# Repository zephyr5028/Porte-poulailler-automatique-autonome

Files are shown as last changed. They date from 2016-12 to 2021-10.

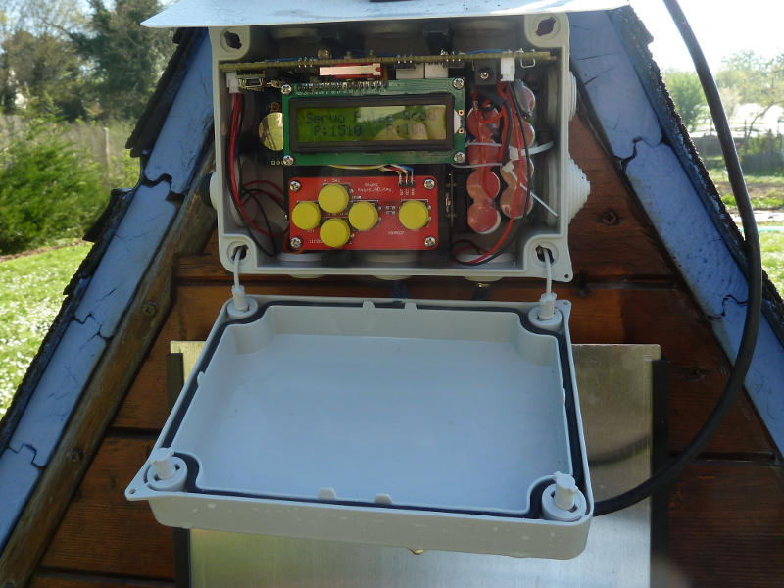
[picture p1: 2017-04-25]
avec encodeur rotatif 3eme version/boitier ouvert.JPG

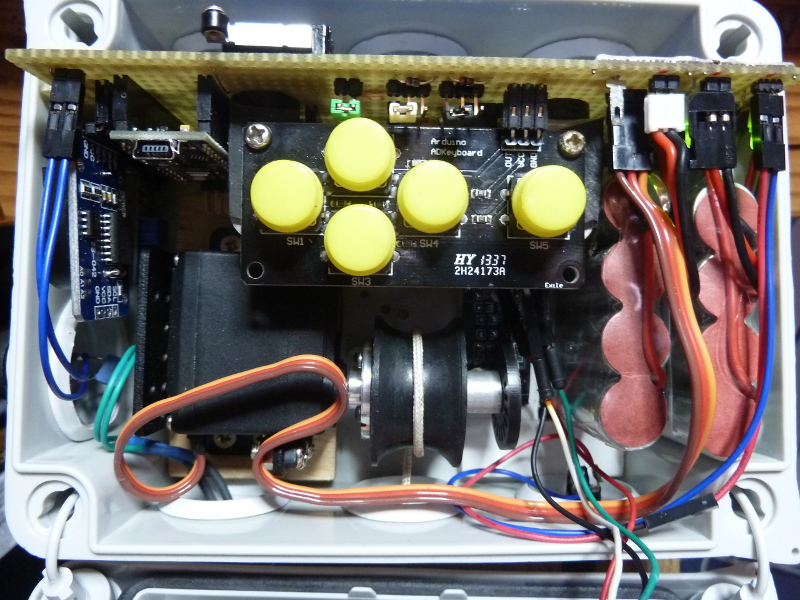
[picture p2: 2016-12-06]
avec roue optique 2eme version/boitier_prototype optique.JPG

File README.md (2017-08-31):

# Porte de poulailler automatique et autonome

Ensemble complet, autonome et reproductible par l'utilisation de l'impression 3D.

Caractéristiques :

Boitier étanche.

Porte coulissante verticale.

Alimentation par un panneau solaire et des batteries NIMH.

Déclenchement automatique de la porte par la lumière ou l’heure.

Réglage de la date et de l’heure.

Réglage de l’heure d’ouverture et de fermeture.

Réglage de la lumière pour l’ouverture et la fermeture.

Choix du type d’ouverture et de fermeture.

Affichage des réglages.

Affichage de la lumière ambiante.

Affichage de la température ambiante.

Choix (interrupteur 4) pour la transmission radio (433,92Mhz) de données de fonctionnement d'une portée d'environ 30m.

(date ; heure ; température ; tension batterie N1 ; tension batterie N2 ; lumière ambiante ; porte ouverte ou fermée ; temps de fonctionnement ; nombre de pas ;)

exemple : 5/7/17;17:4:39;33.75C;5.28V;5.31V;904L;ouv;7644ms;-1P; 

Versions :

1ere version avec un PIC16C84, ne fonctionnant pour l'ouverture/fermeture qu'avec la lumière.

2eme version avec un codeur optique, fonctionnant pour l'ouverture/fermeture avec l'heure et la lumière.

3eme version avec un codeur rotatif et l'intégration dans un boitier étanche IP55 à l'aide d'une imprimante 3D.

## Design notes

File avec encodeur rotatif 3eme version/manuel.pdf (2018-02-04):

04 février 2018

## PORTE DE POULAILLER AUTOMATIQUE

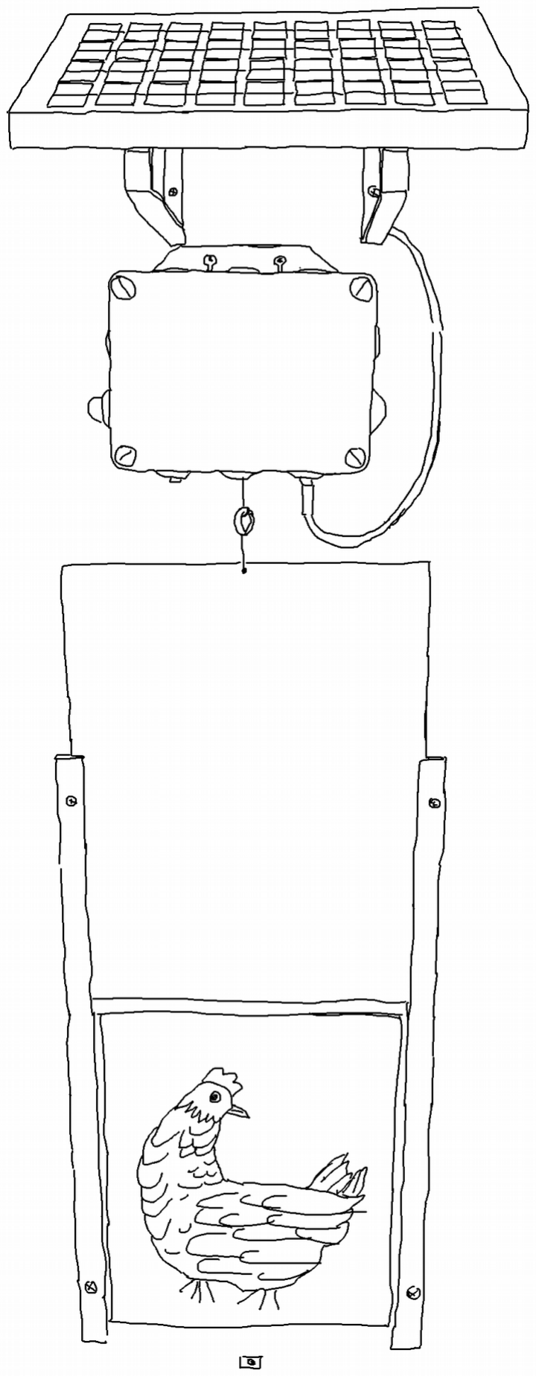
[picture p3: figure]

https://github.com/zephyr5028/Porte-poulailler-automatique | 1 / 12

- Liste du matériel
- 1 panneau solaire avec 2 supports + 4 vis / 4 chevilles.
- 1 porte dans ses 2 glissières + 4 vis / 4 chevilles.
- 1 boîtier électronique complet + 2 crochets / 2 chevilles / une clef.
- 1 protection pluie pour le boîtier.
- 1 bloc secteur 12v.
https://github.com/zephyr5028/Porte-poulailler-automatique | 2 / 12

- Caractéristiques
- Ensemble complètement autonome.
- Déclenchement automatique de la porte par la lumière ou l’heure.
- Alimentation par un panneau solaire.
- Réglage de la date et de l’heure.
- Réglage de l’heure d’ouverture et de fermeture.
- Réglage de la lumière pour l’ouverture et la fermeture.
- Choix du type d’ouverture et de fermeture.
- Affichage des réglages.
- Affichage de la lumière ambiante.
- Affichage de la température ambiante.
- Choix (interrupteur 4) de l’émission radio (433,92Mhz) de données de fonctionnement. -(portée de 30m)

(date ; heure ; température ; tension batterie N1 ; tension batterie N2 ; lumière ambiante ; porte ouverte ou fermée ;
temps de fonctionnement ; nombre de pas ;) | 5/7/17;17:4:39;33.75C;5.28V;5.31V;904L;ouv;7644ms;-1P;
https://github.com/zephyr5028/Porte-poulailler-automatique | 3 / 12

- Présentation du boîtier électronique

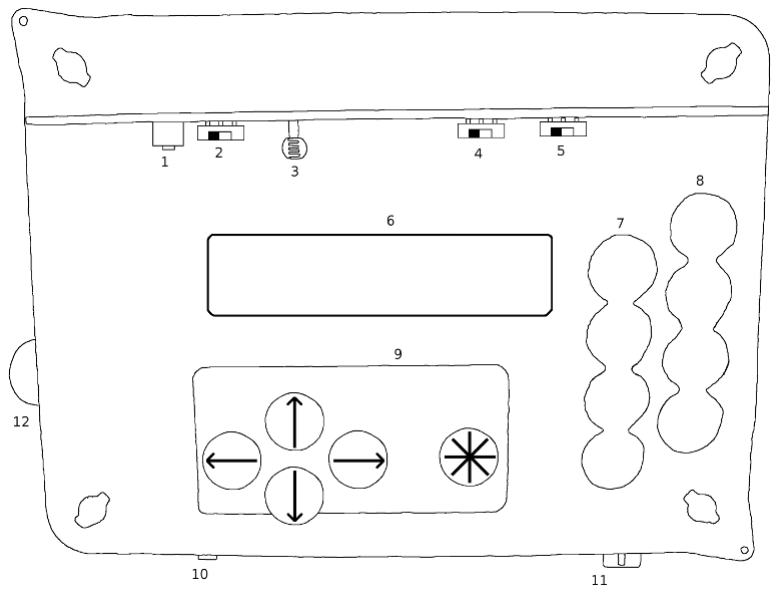
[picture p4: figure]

1 : Bouton poussoir interne pour l’ouverture ou la fermeture de la porte.

2 : Interrupteur de sélection du capteur de lumière externe (position gauche) ou interne.

3 : Capteur de lumière interne.

4 : Interrupteur : On (position droite) / Off de l’ émission de données par radio 433Mhz.

5 : Interrupteur : On (position droite) / Off du fonctionnement du boîtier.

6 : Affichage.

7 : Batterie n°1.

8 : Batterie n°2.

9 : Clavier.

10 : Capteur de lumière externe.

11 : Branchement du panneau solaire.

12 : Bouton poussoir externe pour l’ouverture ou la fermeture de la porte.

https://github.com/zephyr5028/Porte-poulailler-automatique | 4 / 12

- Installation
- - La porte doit toujours glisser librement entre les glissières.
- - Poser l’ensemble glissières et porte avec un niveau
- - Eventuellement utiliser des rondelles pour corriger les défauts du support et éviter la déformation des glissières.
- - fixer l’ensemble glissières avec vis et chevilles.
- - Lever manuellement la porte à son ouverture maximum et positionner le boîtier bien au dessus avec les crochets et chevilles.
- - Mettre en place la protection pluie dans les crochets puis tourner les crochets pour bloquer.
- - Fixer le panneau solaire avec vis et chevilles au dessus du boîtier en vérifiant la disponibilité de la longueur du câble.
- - Brancher le panneau solaire sur la prise 11.
- - Vérifier que les leds vertes sont allumées lorsque le panneau est éclairé.
- - Ouvrir le boîtier avec un tournevis plat. (ne pas forcer sur les quarts de tours)
- - Mettre sous tension (interrupteur 5) , l’aimant monte s’il était descendu.
- - Appuyer su le bouton poussoir 1 ou 12 pour descendre l’aimant.
- - Fixer la cordelette de la porte à l’aimant en gardant 1cm de jeu au dessus de la butée de la porte.
•
- - La cordelette doit toujours rester tendue.
- - Appuyer sur le bouton poussoir pour remonter la porte et vérifier son bon fonctionnement dans les glissières. La porte doit monter juste au dessus du cadre.
- - Renouveler l’opération une fois pour ajuster le réglage de la cordelette.
- - Fermer le boîtier avec un tournevis plat. (ne pas forcer sur les quarts de tours)
- Votre porte est installée.
https://github.com/zephyr5028/Porte-poulailler-automatique | 5 / 12

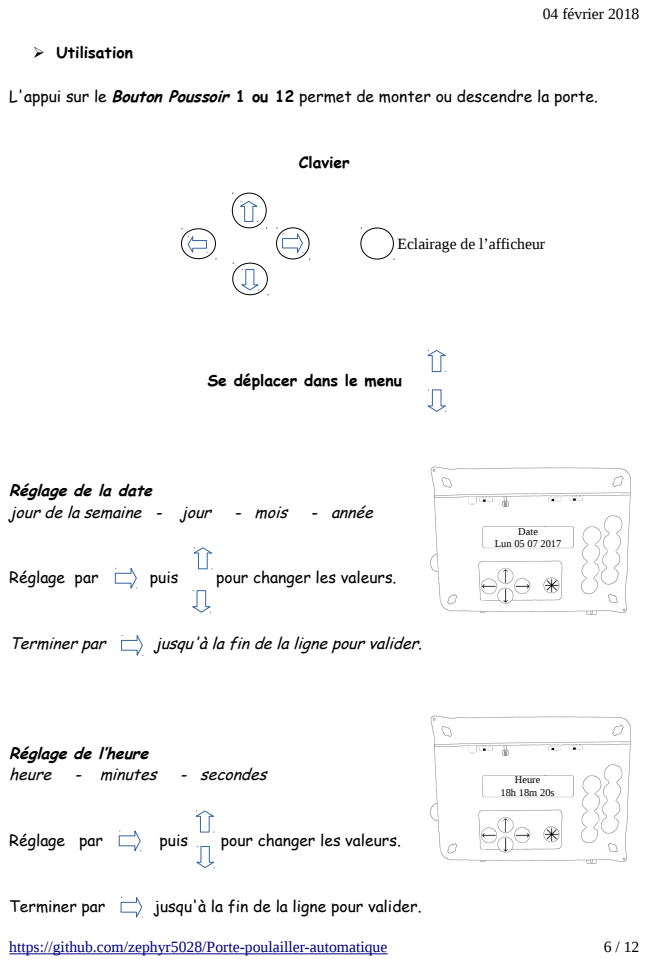
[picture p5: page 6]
➢ Utilisation; Clavier; Réglage par; puis; pour changer les valeurs.; Terminer par; jusqu'à la fin de la ligne pour valider.; https://github.com/zephyr5028/Porte-poulailler-automatique; Date Lun 05 07 2017; Heure 18h 18m 20s

L'appui sur le Bouton Poussoir 1 ou 12 permet de monter ou descendre la porte.

Eclairage de l’afficheur

Se déplacer dans le menu

Réglage de la date
jour de la semaine - jour - mois - année

Réglage de l’heure
heure - minutes - secondes

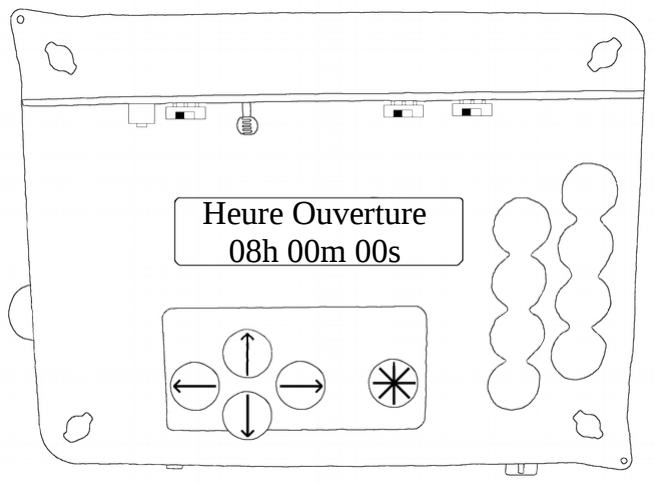
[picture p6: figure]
Heure Ouverture 08h 00m 00s

Réglage de l’heure d’ouverture de la porte
heure - minutes - secondes
Réglage par | puis | pour changer les valeurs.
Terminer par | jusqu'à la fin de la ligne pour valider.

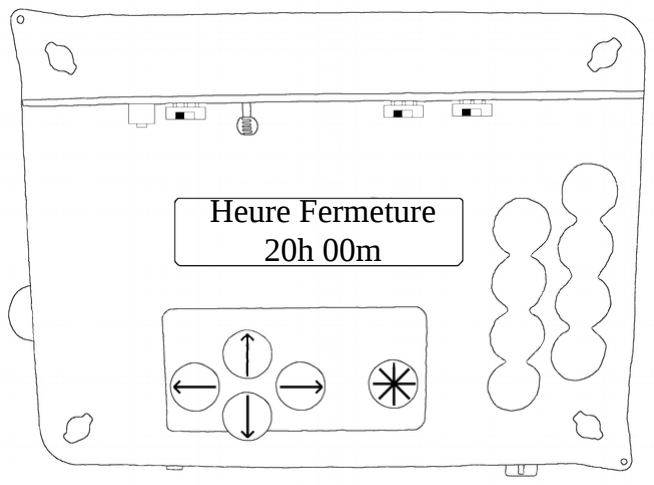
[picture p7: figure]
Heure Fermeture 20h 00m

Réglage de l’heure de fermeture de la porte heure - minutes

Réglage par | puis | pour changer les valeurs.
Terminer par | jusqu'à la fin de la ligne pour valider.

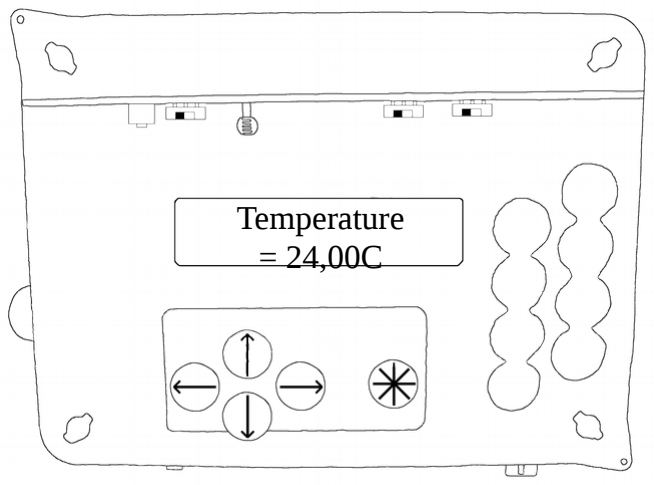
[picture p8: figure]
Temperature = 24,00C

Température ambiante
°Celcius

Capteur de température dans le circuit horloge.

Lumière ambiante
Valeur en Lux

Capteur de lumière (LDR) sous le boitier.

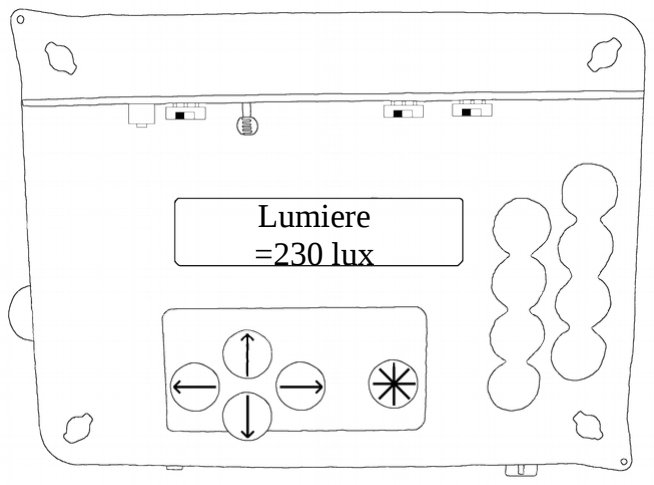
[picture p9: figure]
Lumiere =230 lux

https://github.com/zephyr5028/Porte-poulailler-automatique | 7 / 12

Réglage de la lumière du matin pour l’ouverture de la porte. Valeur en lux

Réglage par | puis | pour changer les valeurs.

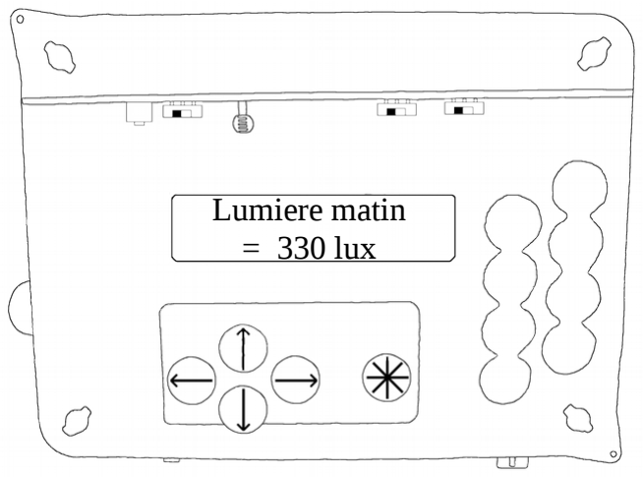
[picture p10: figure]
Lumiere matin = 330 lux

Terminer par | jusqu'à la fin de la ligne pour valider.

Réglage de la lumière du soir pour la fermeture de la porte. Valeur en lux

Réglage par | puis | pour changer les valeurs.

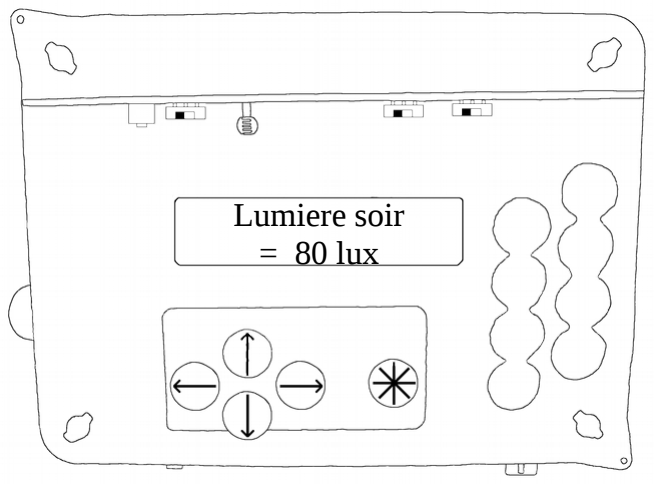
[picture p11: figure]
Lumiere soir = 80 lux

Terminer par | jusqu'à la fin de la ligne pour valider.

Choix pour l'ouverture et la fermeture

choix ouverture : heure ou lumière

choix fermeture : heure ou lumière

Réglage par | puis | pour changer les valeurs.

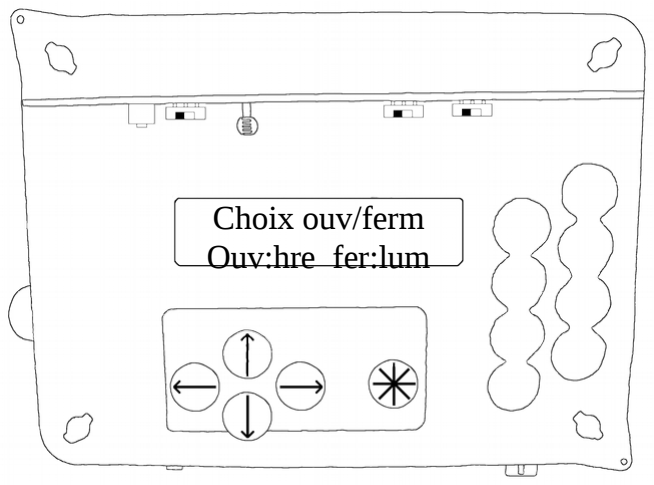
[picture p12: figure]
Choix ouv/ferm Ouv:hre fer:lum

Terminer par | jusqu'à la fin de la ligne pour valider.
https://github.com/zephyr5028/Porte-poulailler-automatique | 8 / 12

Réglage de la fin de course ouverture
(ne pas modifier si possible)
Valeur en pas correspondant à la position (de 0 à 1023)

valeur par défaut = 0 pas (aimant en haut)

Réglage par | puis | pour changer les valeurs.

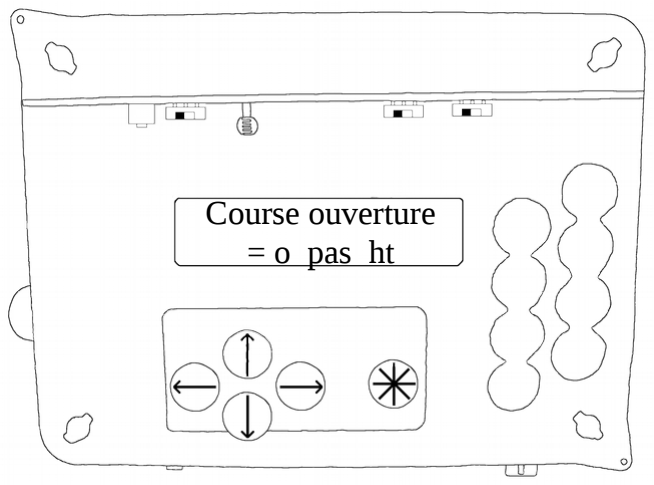
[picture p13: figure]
Course ouverture = o pas ht

Terminer par | jusqu'à la fin de la ligne pour valider.

Réglage de la fin de course fermeture
Valeur en pas correspondant à la position (de 0 à 1023)

valeur par défaut = 65 pas
(ouverture de la porte de 30cm)
Réglage par | puis | pour changer les valeurs.

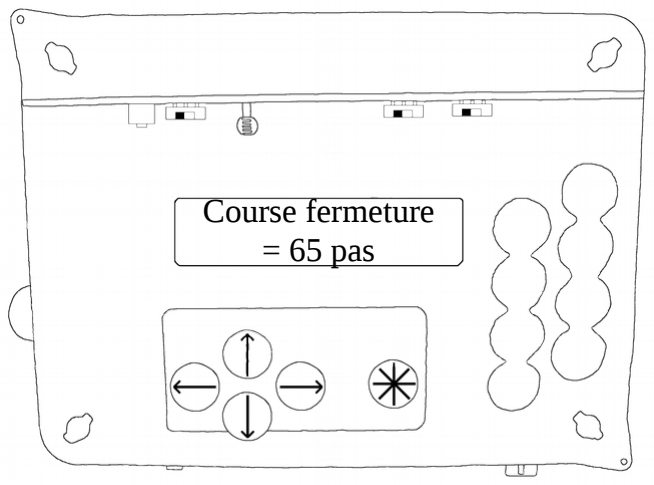
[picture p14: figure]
Course fermeture = 65 pas

Terminer par | jusqu'à la fin de la ligne pour valider.
https://github.com/zephyr5028/Porte-poulailler-automatique | 9 / 12

Tension des batteries N1 et N2
batteries de 4,8v / 2500 mAh chargée : 5,6v / déchargée : 4,4v

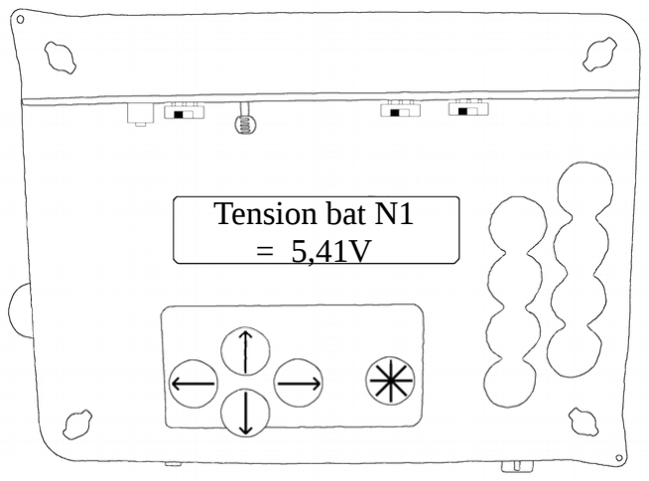
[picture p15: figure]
Tension bat N1 = 5,41V
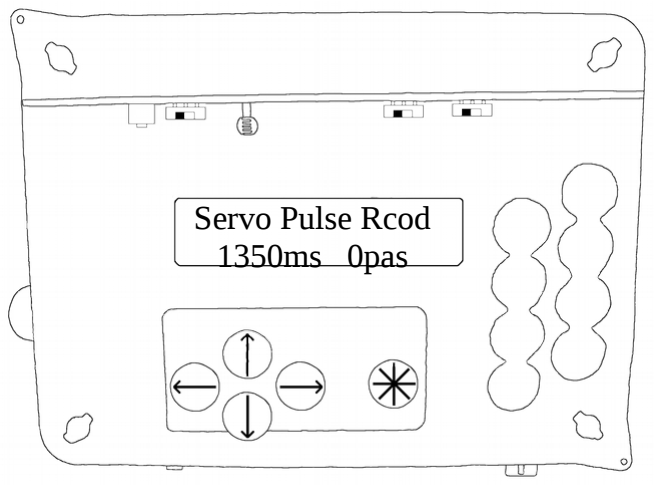
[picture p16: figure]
Servo Pulse Rcod 1350ms 0pas

Servo Pulse Rcod

P : xxxx | R : xxx

P : vitesse du servomoteur en millisecondes R : nombre de pas du servomoteur

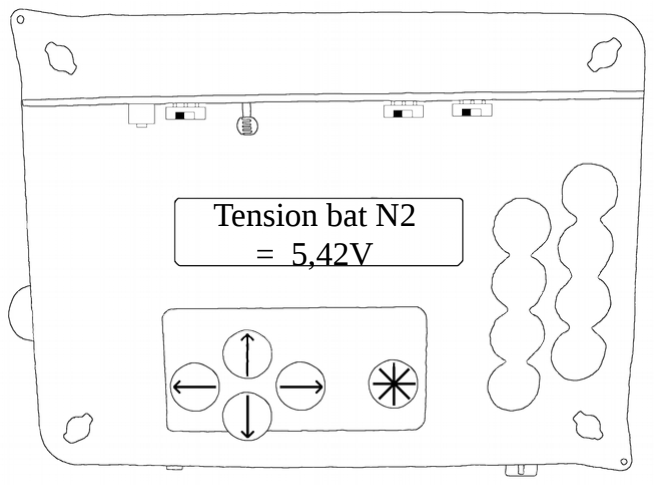
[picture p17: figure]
Tension bat N2 = 5,42V

https://github.com/zephyr5028/Porte-poulailler-automatique | 10 / 12

- Diagnostics en cas de panne
- La porte ne fonctionne plus :
- Les batteries ne sont pas suffisamment chargées par manque de lumière surtout en hiver. Utiliser le bloc secteur de 12volts pour recharger les batteries.
- Vérifier que les leds vertes sont allumées lorsque le panneau solaire est éclairé.
- Le moteur du boîtier force :
- Vérifier que la porte glisse librement dans les glissières.
https://github.com/zephyr5028/Porte-poulailler-automatique | 11 / 12

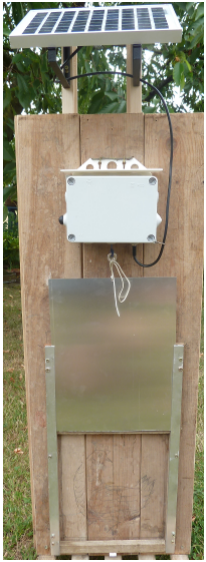
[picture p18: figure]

https://github.com/zephyr5028/Porte-poulailler-automatique | 12 / 12

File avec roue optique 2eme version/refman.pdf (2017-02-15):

## Porte du poulailler automatique

v 1.4.1

### Généré par Doxygen 1.8.11

# Table des matières

1 Porte-poulailler-automatique | 1
2 Index hiérarchique | 3
3 Index des classes | 5
4 Index des fichiers | 7
5 Documentation des classes | 9
5.1.2.1 | Accus(const byte accusPin, const float tensionMiniAccus=4.8, const float

iv | TABLE DES MATIÈRES
5.2.2.2 | Bouton(const byte pinBp, const byte pinBoitier, const int debounce=350, const
5.2.3.1 | testBoitierFerme(const volatile bool &interruptOuvBoi, const bool &boitierOuvert) | 16
5.2.3.2 | testBoitierOuvert(const volatile bool &interruptOuvBoi, const bool &boitierOuvert) 16
5.3.2.2 | Clavier(byte nbMenu, const byte pinBp, const byte pinBoitier, const int de-

Généré par Doxygen

TABLE DES MATIÈRES | v
5.3.3.1 | deplacementDansMenu(const &touche, bool &relache, const bool &reglage) . . 21
5.4.2.1 | Codeur(const byte roueCodeusePin, unsigned int finDeCourseFermeture=250, unsigned int finDeCourseOuverture=150, unsigned int compteRoue←-

vi | TABLE DES MATIÈRES
5.5.2.2 | HorlogeDS3232(const byte adresseMemoireI2C=0x57, const byte m_rtcINT=5,
5.5.3.3 | choixTypeOuvertureFermeture(bool choixOuvertureFermeture, const byte alarme) 34

TABLE DES MATIÈRES | vii

5.5.3.18 sauvEepromChoix(unsigned int valeurChoix, const bool matinSoirOuvFerm,

5.6.3.2 | affichageDateHeure(String jourSemaine, byte jourHeure, byte moisMinute, byte
5.6.3.3 | affichageLumFinCourse(unsigned int lum, byte ligne, bool siNonReglable=0) . . 46

viii | TABLE DES MATIÈRES

5.6.3.10 cursorPositionReglages(const byte &touche, bool &relache, bool &reglage, const

5.7.2.1 | LcdPCF8574(char, const byte taille=16, const byte nbLigne=2, boolean de-
5.7.3.2 | affichageDateHeure(String jourSemaine, byte jourHeure, byte moisMinute, byte
5.7.3.3 | affichageLumFinCourse(unsigned int lum, byte ligne, bool siNonReglable=0) . . 56

TABLE DES MATIÈRES | ix

5.7.3.10 cursorPositionReglages(const byte &touche, bool &relache, bool &reglage, const

5.8.2.1 Lumiere(const byte lumierePin, unsigned int lumMatin, unsigned int lumSoir, const byte heureFenetreSoir=17, const float rapportConvertion=5, const byte temps←-

x | TABLE DES MATIÈRES
5.8.3.9 | nonDeclenchementPositionServo(volatile unsigned int compteRoueCodeuse, un-

5.8.3.11 set_m_compteurWatchdogLumiere(unsigned int compteurWatchdogLumiere) . . 69

TABLE DES MATIÈRES | xi
5.9 Référence de la classe PowerTools | 73
5.9.1 Description détaillée | 74
5.9.2 Documentation des constructeurs et destructeur | 74
5.9.2.1 | PowerTools() | 74
5.9.2.2 | PowerTools(const boolean debug=false) | 74
5.9.2.3 | ∼PowerTools() | 74
5.9.3 Documentation des fonctions membres | 75
5.9.3.1 | setup_watchdog(int parametreTemps) | 75
5.9.3.2 | setupPower() | 75
5.9.3.3 | tailleChaine(char ∗chaine) | 75
5.9.4 Documentation des données membres | 76
5.9.4.1 m_debug | 76
5.10 Référence de la classe Radio | 76
5.10.1 Description détaillée | 77
5.10.2 Documentation des constructeurs et destructeur | 77

5.10.2.1 Radio(byte pinEmRadio, byte pinSwitchEmissionRadio, int vitesseTransmission,
| byte taille, boolean radio=false, boolean debug=false) | 77
5.10.2.2 ∼Radio() | 77
5.10.3 Documentation des fonctions membres | 78
5.10.3.1 chaineVide() | 78
5.10.3.2 envoiFloat(float valeur, boolean boitierOuvert=true, char ∗texte="""") | 78
5.10.3.3 envoiMessage(char ∗chaine1) | 79

5.10.3.4 envoiUnsignedInt(unsigned int valeur, boolean boitierOuvert=true, char ∗texte="""") 80

5.10.3.5 get_m_radio() | 80
5.10.3.6 init() | 81
5.10.3.7 messageRadio(char ∗chaine1) | 81
5.10.3.8 messageSansParametre() | 82
5.10.3.9 raz_m_chaine() | 82
5.10.3.10 set_m_radio(bool radio) | 83
5.10.3.11 testSwitchEmissionRadio() | 83
5.10.4 Documentation des données membres | 83

xii | TABLE DES MATIÈRES
5.10.4.1 m_chaine | 83
5.10.4.2 m_debug | 83
5.10.4.3 m_pinEmRadio | 83
5.10.4.4 m_pinSwitchEmissionRadio | 84
5.10.4.5 m_radio | 84
5.10.4.6 m_taille | 84
5.10.4.7 m_vitesseTransmission | 84
5.11 Référence de la classe ServoMoteur | 84
5.11.1 Description détaillée | 87
5.11.2 Documentation des constructeurs et destructeur | 87
5.11.2.1 ServoMoteur(const byte pinCde, const byte pinRelais, const byte pinSecurite←-Haute, const int pulseStop=1500, const int pulseOuvFerm=140, const int pulse←-
Reduit=70, boolean debug=false) | 87
5.11.2.2 ∼ServoMoteur() | 87
5.11.3 Documentation des fonctions membres | 88
5.11.3.1 get_m_ouvFerm() | 88
5.11.3.2 get_m_pulse() | 88
5.11.3.3 get_m_servoAction() | 88
5.11.3.4 init() | 89
5.11.3.5 modificationVitesse(bool reduit) | 89
5.11.3.6 relaisHorsTension() | 90
5.11.3.7 relaisSousTension() | 90
5.11.3.8 servoHorsTension(unsigned int compteRoueCodeuse, unsigned int finCourse←-
Ouverture) | 91
5.11.3.9 servoOuvFerm(bool batterieFaible, bool reduit) | 92
5.11.3.10 servoVitesse(bool reduit) | 92
5.11.3.11 set_m_ouvFerm(bool ouvFerm) | 93
5.11.3.12 set_m_pulse(int pulse) | 94
5.11.3.13 set_m_servoAction(bool servoAction) | 94
5.11.4 Documentation des données membres | 94
5.11.4.1 m_debug | 94
5.11.4.2 m_ouvFerm | 94
5.11.4.3 m_pinCde | 94
5.11.4.4 m_pinRelais | 94
5.11.4.5 m_pinSecuriteHaute | 94
5.11.4.6 m_pulse | 94
5.11.4.7 m_pulseOuvFerm | 95
5.11.4.8 m_pulseReduit | 95
5.11.4.9 m_pulseStop | 95
5.11.4.10 m_servoAction | 95

TABLE DES MATIÈRES | xiii
6 Documentation des fichiers | 97

6.1 Référence du fichier /home/jlm-atelier/Bureau/GIT/Porte-poulailler-automatique/carte heuristique

6.2 Référence du fichier /home/jlm-atelier/Bureau/GIT/Porte-poulailler-automatique/porte_poulailler_←-

6.3 Référence du fichier /home/jlm-atelier/Bureau/GIT/Porte-poulailler-automatique/porte_poulailler_←-

xiv | TABLE DES MATIÈRES
6.3.1.25 openTime() | 115
6.3.1.26 ouverturePorte() | 116
6.3.1.27 ouvFermLum() | 117
6.3.1.28 read_temp(const boolean typeTemperature) | 118
6.3.1.29 regFinDeCourseFermeture() | 119
6.3.1.30 regFinDeCourseOuverture() | 120
6.3.1.31 reglageDate() | 120
6.3.1.32 reglageHeureFermeture() | 121
6.3.1.33 reglageHeureOuverture() | 121
6.3.1.34 reglageTime() | 122
6.3.1.35 routineGestionWatchdog() | 123
6.3.1.36 routineInterrruptionAlarme2() | 123
6.3.1.37 routineInterruptionAlarme1() | 124
6.3.1.38 routineInterruptionBp() | 125
6.3.1.39 routineTestFermetureBoitier() | 125
6.3.1.40 routineTestOuvertureBoitier() | 126
6.3.1.41 temporisationAffichage(const int boucleTemps) | 126
6.3.1.42 testServo() | 127

6.4 Référence du fichier /home/jlm-atelier/Bureau/GIT/Porte-poulailler-automatique/porte_poulailler_←-
affichage_clavier_rtc/Accus.cpp | 128

6.5 Référence du fichier /home/jlm-atelier/Bureau/GIT/Porte-poulailler-automatique/porte_poulailler_←-
affichage_clavier_rtc/Accus.h | 128

6.6 Référence du fichier /home/jlm-atelier/Bureau/GIT/Porte-poulailler-automatique/porte_poulailler_←-
affichage_clavier_rtc/Bouton.cpp | 129

6.7 Référence du fichier /home/jlm-atelier/Bureau/GIT/Porte-poulailler-automatique/porte_poulailler_←-
affichage_clavier_rtc/Bouton.h | 130

6.8 Référence du fichier /home/jlm-atelier/Bureau/GIT/Porte-poulailler-automatique/porte_poulailler_←-
affichage_clavier_rtc/Clavier.cpp | 131

6.9 Référence du fichier /home/jlm-atelier/Bureau/GIT/Porte-poulailler-automatique/porte_poulailler_←-
affichage_clavier_rtc/Clavier.h | 132

6.10 Référence du fichier /home/jlm-atelier/Bureau/GIT/Porte-poulailler-automatique/porte_poulailler_←-
affichage_clavier_rtc/Codeur.cpp | 133

6.11 Référence du fichier /home/jlm-atelier/Bureau/GIT/Porte-poulailler-automatique/porte_poulailler_←-
affichage_clavier_rtc/Codeur.h | 133

TABLE DES MATIÈRES | xv

6.12 Référence du fichier /home/jlm-atelier/Bureau/GIT/Porte-poulailler-automatique/porte_poulailler_←-
affichage_clavier_rtc/HorlogeDS3232.cpp | 134

6.13 Référence du fichier /home/jlm-atelier/Bureau/GIT/Porte-poulailler-automatique/porte_poulailler_←-
affichage_clavier_rtc/HorlogeDS3232.h | 135
6.13.1 Documentation des macros | 136
6.13.1.1 DS3231_I2C_ADDRESS | 136

6.14 Référence du fichier /home/jlm-atelier/Bureau/GIT/Porte-poulailler-automatique/porte_poulailler_←-
affichage_clavier_rtc/LcdDigoleI2C.cpp | 136

6.15 Référence du fichier /home/jlm-atelier/Bureau/GIT/Porte-poulailler-automatique/porte_poulailler_←-
affichage_clavier_rtc/LcdDigoleI2C.h | 136
6.15.1 Documentation des macros | 137
6.15.1.1 _Digole_Serial_I2C_ | 137

6.16 Référence du fichier /home/jlm-atelier/Bureau/GIT/Porte-poulailler-automatique/porte_poulailler_←-
affichage_clavier_rtc/LcdPCF8574.cpp | 138

6.17 Référence du fichier /home/jlm-atelier/Bureau/GIT/Porte-poulailler-automatique/porte_poulailler_←-
affichage_clavier_rtc/LcdPCF8574.h | 138

6.18 Référence du fichier /home/jlm-atelier/Bureau/GIT/Porte-poulailler-automatique/porte_poulailler_←-
affichage_clavier_rtc/Lumiere.cpp | 139

6.19 Référence du fichier /home/jlm-atelier/Bureau/GIT/Porte-poulailler-automatique/porte_poulailler_←-
affichage_clavier_rtc/Lumiere.h | 140

6.20 Référence du fichier /home/jlm-atelier/Bureau/GIT/Porte-poulailler-automatique/porte_poulailler_←-
affichage_clavier_rtc/porte_poulailler_affichage_clavier_rtc.ino | 140
6.20.1 Documentation des macros | 144
6.20.1.1 LCD_DIGOLE | 144
6.20.1.2 LED_PIN | 144
6.20.2 Documentation des fonctions | 144
6.20.2.1 affichageDemarrage(byte colonne) | 144
6.20.2.2 affiChoixOuvFerm() | 145
6.20.2.3 affiFinDeCourseFermeture() | 145
6.20.2.4 affiFinDeCourseOuverture() | 146
6.20.2.5 affiLumMatin() | 147
6.20.2.6 affiLumSoir() | 147
6.20.2.7 affiPulsePlusCptRoue() | 148
6.20.2.8 affiTensionBatCdes() | 149

xvi | TABLE DES MATIÈRES

TABLE DES MATIÈRES | xvii
6.20.2.39 routineInterruptionAlarme1() | 170
6.20.2.40 routineInterruptionBp() | 171
6.20.2.41 routineTestFermetureBoitier() | 171
6.20.2.42 routineTestOuvertureBoitier() | 172
6.20.2.43 setup() | 172
6.20.2.44 temporisationAffichage(const int boucleTemps) | 173
6.20.2.45 testServo() | 174
6.20.3 Documentation des variables | 175
6.20.3.1 accusCde | 175
6.20.3.2 accusPinCde | 175
6.20.3.3 accusPinServo | 175
6.20.3.4 accusServo | 175
6.20.3.5 adresseBoitier24C32 | 175
6.20.3.6 alarm_1 | 175
6.20.3.7 alarm_2 | 175
6.20.3.8 annee | 176
6.20.3.9 batterieFaible | 176
6.20.3.10 boitierOuvert | 176
6.20.3.11 boucleLumiere | 176
6.20.3.12 bouclesWatchdog | 176
6.20.3.13 boucleTemps | 176
6.20.3.14 clav | 176
6.20.3.15 codOpt | 176
6.20.3.16 colonnes | 176
6.20.3.17 compteRoueCodeuse | 176
6.20.3.18 convertion | 176
6.20.3.19 debounce | 177
6.20.3.20 debug | 177
6.20.3.21 emissionRadio | 177
6.20.3.22 f_wdt | 177

xviii | TABLE DES MATIÈRES
6.20.3.23 finDeCourseFermeture | 177
6.20.3.24 finDeCourseOuverture | 177
6.20.3.25 heure | 177
6.20.3.26 heureFenetreSoir | 177
6.20.3.27 incrementation | 177
6.20.3.28 interruptBp | 178
6.20.3.29 interruptOuvBoi | 178
6.20.3.30 interruptRTC | 178
6.20.3.31 jour | 178
6.20.3.32 jourSemaine | 178
6.20.3.33 LcdCursor | 178
6.20.3.34 lum | 178
6.20.3.35 lumierePin | 178
6.20.3.36 lumMatin | 178
6.20.3.37 lumSoir | 178
6.20.3.38 memoireLibre | 179
6.20.3.39 menuChoix | 179
6.20.3.40 menuDate | 179
6.20.3.41 menuFermeture | 179
6.20.3.42 menuFinDeCourseFermeture | 179
6.20.3.43 menuFinDeCourseOuverture | 179
6.20.3.44 menuHeure | 179
6.20.3.45 menuLumiere | 179
6.20.3.46 menuLumiereMatin | 179
6.20.3.47 menuLumiereSoir | 179
6.20.3.48 menuManuel | 180
6.20.3.49 menuOuverture | 180
6.20.3.50 menuTemperature | 180
6.20.3.51 menuTensionBatCdes | 180
6.20.3.52 menuTensionBatServo | 180

TABLE DES MATIÈRES | xix
6.20.3.53 minutes | 180
6.20.3.54 mois | 180
6.20.3.55 monServo | 180
6.20.3.56 oldkey | 180
6.20.3.57 pinBoitier | 180
6.20.3.58 pinBp | 180
6.20.3.59 pinEmRadio | 181
6.20.3.60 pinSwitchEmissionRadio | 181
6.20.3.61 PROGMEM | 181
6.20.3.62 pulseStop | 181
6.20.3.63 radio | 181
6.20.3.64 rapportConvertion | 181
6.20.3.65 reduit | 181
6.20.3.66 reglage | 181
6.20.3.67 relache | 181
6.20.3.68 roueCodeuse | 181
6.20.3.69 rtc | 182
6.20.3.70 rtcINT | 182
6.20.3.71 secondes | 182
6.20.3.72 securiteHaute | 182
6.20.3.73 sensorClavier | 182
6.20.3.74 servoCde | 182
6.20.3.75 servoPin | 182
6.20.3.76 temps | 182
6.20.3.77 tempsWatchdog | 182
6.20.3.78 tensionMiniAccus | 182
6.20.3.79 testServoMoteur | 183
6.20.3.80 tm | 183
6.20.3.81 tools | 183
6.20.3.82 touche | 183

xx | TABLE DES MATIÈRES
6.20.3.83 typeTemperature | 183
6.20.3.84 vitesseTransmission | 183
6.20.3.85 Wire | 183

6.21 Référence du fichier /home/jlm-atelier/Bureau/GIT/Porte-poulailler-automatique/porte_poulailler_←-
affichage_clavier_rtc/PowerTools.cpp | 183

6.22 Référence du fichier /home/jlm-atelier/Bureau/GIT/Porte-poulailler-automatique/porte_poulailler_←-
affichage_clavier_rtc/PowerTools.h | 184

6.23 Référence du fichier /home/jlm-atelier/Bureau/GIT/Porte-poulailler-automatique/porte_poulailler_←-
affichage_clavier_rtc/Radio.cpp | 184

6.24 Référence du fichier /home/jlm-atelier/Bureau/GIT/Porte-poulailler-automatique/porte_poulailler_←-
affichage_clavier_rtc/Radio.h | 185

6.25 Référence du fichier /home/jlm-atelier/Bureau/GIT/Porte-poulailler-automatique/porte_poulailler_←-
affichage_clavier_rtc/ServoMoteur.cpp | 186

6.26 Référence du fichier /home/jlm-atelier/Bureau/GIT/Porte-poulailler-automatique/porte_poulailler_←-
affichage_clavier_rtc/ServoMoteur.h | 187

6.27 Référence du fichier /home/jlm-atelier/Bureau/GIT/Porte-poulailler-automatique/README.md . . . 187

Index | 189

## Chapitre 1

# Porte-poulailler-automatique

Automatisation de la porte de mon poulailler. Déclenchement par la lumière ou l'heure.

### 2 Porte-poulailler-automatique

## Chapitre 2

# Index hiérarchique

### 2.1 Hiérarchie des classes

Cette liste d'héritage est classée approximativement par ordre alphabétique :

Accus | | 9
Bouton | | 13
Clavier | 19
Codeur | 24
DigoleSerialDisp
LcdDigoleI2C | 42
DS3232RTC
HorlogeDS3232 | 30
LiquidCrystal_I2C
LcdPCF8574 | 53
Lumiere | | 63
PowerTools | | 73
Radio | | 76
ServoTimer2
ServoMoteur | 84

### 4 Index hiérarchique

## Chapitre 3

# Index des classes

### 3.1 Liste des classes

Liste des classes, structures, unions et interfaces avec une brève description :

Accus
Gestion des blocs accumulateurs NIMH de 4,8v | ??
Bouton | ??
Clavier | ??
Codeur | ??
HorlogeDS3232 | ??
LcdDigoleI2C | ??
LcdPCF8574 | ??
Lumiere | ??
PowerTools | ??
Radio | ??
ServoMoteur | ??

### 6 Index des classes

## Chapitre 4

# Index des fichiers

### 4.1 Liste des fichiers

Liste de tous les fichiers avec une brève description :

/home/jlm-atelier/Bureau/GIT/Porte-poulailler-automatique/carte heuristique porte poulailler.mm . . . ?? /home/jlm-atelier/Bureau/GIT/Porte-poulailler-automatique/porte_poulailler_affichage_clavier_rtc/AA_←-
fonctions.cpp | ??
/home/jlm-atelier/Bureau/GIT/Porte-poulailler-automatique/porte_poulailler_affichage_clavier_rtc/AA_←-
fonctions.h | ??
/home/jlm-atelier/Bureau/GIT/Porte-poulailler-automatique/porte_poulailler_affichage_clavier_rtc/Accus.←-
cpp | ??
/home/jlm-atelier/Bureau/GIT/Porte-poulailler-automatique/porte_poulailler_affichage_clavier_rtc/Accus.←-
h | ??
/home/jlm-atelier/Bureau/GIT/Porte-poulailler-automatique/porte_poulailler_affichage_clavier_rtc/Bouton.←-
cpp | ??
/home/jlm-atelier/Bureau/GIT/Porte-poulailler-automatique/porte_poulailler_affichage_clavier_rtc/Bouton.←-
h | ??
/home/jlm-atelier/Bureau/GIT/Porte-poulailler-automatique/porte_poulailler_affichage_clavier_rtc/Clavier.←-
cpp | ??
/home/jlm-atelier/Bureau/GIT/Porte-poulailler-automatique/porte_poulailler_affichage_clavier_rtc/Clavier.←-
h | ??
/home/jlm-atelier/Bureau/GIT/Porte-poulailler-automatique/porte_poulailler_affichage_clavier_rtc/Codeur.←-
cpp | ??
/home/jlm-atelier/Bureau/GIT/Porte-poulailler-automatique/porte_poulailler_affichage_clavier_rtc/Codeur.←-
h | ??
/home/jlm-atelier/Bureau/GIT/Porte-poulailler-automatique/porte_poulailler_affichage_clavier_rtc/Horloge←-
DS3232.cpp | ??
/home/jlm-atelier/Bureau/GIT/Porte-poulailler-automatique/porte_poulailler_affichage_clavier_rtc/Horloge←-
DS3232.h | ??
/home/jlm-atelier/Bureau/GIT/Porte-poulailler-automatique/porte_poulailler_affichage_clavier_rtc/Lcd←-
DigoleI2C.cpp | ??
/home/jlm-atelier/Bureau/GIT/Porte-poulailler-automatique/porte_poulailler_affichage_clavier_rtc/Lcd←-
DigoleI2C.h | ??
/home/jlm-atelier/Bureau/GIT/Porte-poulailler-automatique/porte_poulailler_affichage_clavier_rtc/LcdP←-
CF8574.cpp | ??
/home/jlm-atelier/Bureau/GIT/Porte-poulailler-automatique/porte_poulailler_affichage_clavier_rtc/LcdP←-
CF8574.h | ??
/home/jlm-atelier/Bureau/GIT/Porte-poulailler-automatique/porte_poulailler_affichage_clavier_rtc/Lumiere.←-
cpp | ??

### 8 Index des fichiers

/home/jlm-atelier/Bureau/GIT/Porte-poulailler-automatique/porte_poulailler_affichage_clavier_rtc/Lumiere.←-
h | ??
/home/jlm-atelier/Bureau/GIT/Porte-poulailler-automatique/porte_poulailler_affichage_clavier_rtc/porte←-
_poulailler_affichage_clavier_rtc.ino | ??
/home/jlm-atelier/Bureau/GIT/Porte-poulailler-automatique/porte_poulailler_affichage_clavier_rtc/Power←-
Tools.cpp | ??
/home/jlm-atelier/Bureau/GIT/Porte-poulailler-automatique/porte_poulailler_affichage_clavier_rtc/Power←-
Tools.h | ??
/home/jlm-atelier/Bureau/GIT/Porte-poulailler-automatique/porte_poulailler_affichage_clavier_rtc/Radio.←-
cpp | ??
/home/jlm-atelier/Bureau/GIT/Porte-poulailler-automatique/porte_poulailler_affichage_clavier_rtc/Radio.←-
h | ??
/home/jlm-atelier/Bureau/GIT/Porte-poulailler-automatique/porte_poulailler_affichage_clavier_rtc/Servo←-
Moteur.cpp | ??
/home/jlm-atelier/Bureau/GIT/Porte-poulailler-automatique/porte_poulailler_affichage_clavier_rtc/Servo←-
Moteur.h | ??

## Chapitre 5

# Documentation des classes

### 5.1 Référence de la classe Accus

Gestion des blocs accumulateurs NIMH de 4,8v.

#include <Accus.h>

Graphe de collaboration de Accus :

Accus
# m_debug

# m_accusPin

# m_rapportConvertion

# m_maxCAD

# m_tensionMiniAccus

+ Accus()
+ ~Accus()
+ accusFaible()
+ tensionAccusCAD()
+ tensionAccus()
+ tensionAccusCADversFloat()

Fonctions membres publiques
— Accus (const byte accusPin, const float tensionMiniAccus=4.8, const float rapportConvertion=7.5, boolean debug=false)
— ∼Accus ()
— bool accusFaible ()

teste si la tension est faible
— int tensionAccusCAD ()

----— lecture tension batterie CAD--—
— float tensionAccus (int valAccus)

----— convertion CAD vers tension batterie --—
— float tensionAccusCADversFloat ()

--—lecture et convertion vers tension batterie en float--—

### 10 Documentation des classes

Attributs protégés

— const boolean m_debug
— const byte m_accusPin
— const float m_rapportConvertion
— const int m_maxCAD
— const float m_tensionMiniAccus

### 5.1.1 Description détaillée

Gestion des blocs accumulateurs NIMH de 4,8v.

Suivi de la tension et la valeur minimum

Auteur
Zephyr5028

Date
hiver 2017 Prototype de la classe Accus (p. ??)

Définition à la ligne 16 du fichier Accus.h.

### 5.1.2 Documentation des constructeurs et destructeur

5.1.2.1 Accus : :Accus ( const byte accusPin, const float tensionMiniAccus = 4.8, const float rapportConvertion = 7.5, boolean debug = false )

Accus.cpp (p. ??) définitions de la classe Accus (p. ??) bloc accus NIMH

Définition à la ligne 9 du fichier Accus.cpp.

### 5.1.2.2 Accus : :∼Accus ( )

Définition à la ligne 14 du fichier Accus.cpp.

### 5.1.3 Documentation des fonctions membres

### 5.1.3.1 bool Accus : :accusFaible ( )

teste si la tension est faible

Lecture et conversion de la valeur mesurée sur un pont de résistances en parallèle de l'accu

Paramètres
m_accusPin numéro de l'entrée analogique

5.1 Référence de la classe Accus | 11

Renvoie
batterieFaible si < 4,8v

convertion tension mini en pas du CAD

read the input on analog pin tension batterie

si la batterie est faible < 4,8v (654)

Définition à la ligne 24 du fichier Accus.cpp.

Voici le graphe des appelants de cette fonction :

Accus::accusFaible | loop

### 5.1.3.2 float Accus : :tensionAccus ( int valAccus )

----— convertion CAD vers tension batterie --—

Définition à la ligne 42 du fichier Accus.cpp.

Voici le graphe des appelants de cette fonction :

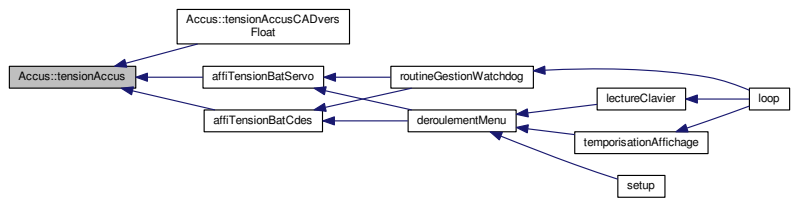
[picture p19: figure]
Accus::tensionAccus; Accus::tensionAccusCADvers Float; affiTensionBatCdes; affiTensionBatServo; deroulementMenu; routineGestionWatchdog; lectureClavier; temporisationAffichage; setup; loop

### 5.1.3.3 int Accus : :tensionAccusCAD ( )

----— lecture tension batterie CAD--—

Définition à la ligne 36 du fichier Accus.cpp.

### 12 Documentation des classes

Voici le graphe des appelants de cette fonction :

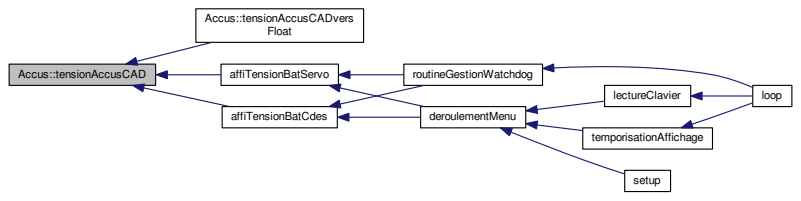
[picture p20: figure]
Accus::tensionAccusCAD; Accus::tensionAccusCADvers Float; affiTensionBatCdes; affiTensionBatServo; deroulementMenu; routineGestionWatchdog; lectureClavier; temporisationAffichage; setup; loop

### 5.1.3.4 float Accus : :tensionAccusCADversFloat ( )

--—lecture et convertion vers tension batterie en float--—

Définition à la ligne 49 du fichier Accus.cpp.

Voici le graphe d'appel pour cette fonction :

Accus::tensionAccusCADvers Float

Accus::tensionAccus

Accus::tensionAccusCAD

### 5.1.4 Documentation des données membres

### 5.1.4.1 const byte Accus : :m_accusPin [protected]

Définition à la ligne 33 du fichier Accus.h.

### 5.1.4.2 const boolean Accus : :m_debug [protected]

Définition à la ligne 32 du fichier Accus.h.

### 5.1.4.3 const int Accus : :m_maxCAD [protected]

Définition à la ligne 36 du fichier Accus.h.

5.2 Référence de la classe Bouton | 13

### 5.1.4.4 const float Accus : :m_rapportConvertion [protected]

Définition à la ligne 35 du fichier Accus.h.

### 5.1.4.5 const float Accus : :m_tensionMiniAccus [protected]

Définition à la ligne 37 du fichier Accus.h.

La documentation de cette classe a été générée à partir des fichiers suivants :

— /home/jlm-atelier/Bureau/GIT/Porte-poulailler-automatique/porte_poulailler_affichage_clavier_rtc/Accus.h — /home/jlm-atelier/Bureau/GIT/Porte-poulailler-automatique/porte_poulailler_affichage_clavier_rtc/Accus.←-
cpp

### 5.2 Référence de la classe Bouton

#include <Bouton.h>

### 14 Documentation des classes

Graphe d'héritage de Bouton :

Bouton
# m_debug

# m_pinBp

# m_pinBoitier

# m_debounce

# m_tempoDebounce

# m_relacheBp

+ Bouton()
+ Bouton()
+ ~Bouton()
+ testToucheBp()
+ testRelacheBp()
+ testInterruptionBp()
+ testInterruptionBoitier() + testBoitierOuvert()
+ testBoitierFerme()

Clavier
# m_debug

# m_oldKey

# m_NumKeys

# m_MenuManuel

# m_AdcKeyVal

+ Clavier()
+ Clavier()
+ ~Clavier()
+ get_key()
+ read_key()
+ positionMenu()
+ deplacementDansMenu()
+ relacheTouche()
+ testTouche5() | Généré par Doxygen

5.2 Référence de la classe Bouton | 15

Graphe de collaboration de Bouton :

Bouton
# m_debug

# m_pinBp

# m_pinBoitier

# m_debounce

# m_tempoDebounce

# m_relacheBp

+ Bouton()
+ Bouton()
+ ~Bouton()
+ testToucheBp()
+ testRelacheBp()
+ testInterruptionBp()
+ testInterruptionBoitier() + testBoitierOuvert()
+ testBoitierFerme()

Fonctions membres publiques

— Bouton ()
— Bouton (const byte pinBp, const byte pinBoitier, const int debounce=350, const boolean debug=false)
— ∼Bouton ()
— bool testToucheBp ()

--—test touche Bp--—
— void testRelacheBp (volatile bool &interruptBp)

--—test relache Bp--—
— void testInterruptionBp (volatile bool &interruptBp)

--—test IT Bp--—
— void testInterruptionBoitier (volatile bool &interruptOuvBoi)

--—test IT ouverture boitier--—
— bool testBoitierOuvert (const volatile bool &interruptOuvBoi, const bool &boitierOuvert)

--—test boitier ouvert---—
— bool testBoitierFerme (const volatile bool &interruptOuvBoi, const bool &boitierOuvert)

--—test boitier ferme---—

Attributs protégés

— const boolean m_debug
— const byte m_pinBp
— const byte m_pinBoitier
— const int m_debounce
— int m_tempoDebounce
— bool m_relacheBp

### 5.2.1 Description détaillée

Bouton.h (p. ??) prototype de la Bouton (p. ??)

Définition à la ligne 10 du fichier Bouton.h.

### 16 Documentation des classes

### 5.2.2 Documentation des constructeurs et destructeur

### 5.2.2.1 Bouton : :Bouton ( )

Bouton.cpp (p. ??) définitions de la classe Bouton (p. ??)

Définition à la ligne 7 du fichier Bouton.cpp.

5.2.2.2 Bouton : :Bouton ( const byte pinBp, const byte pinBoitier, const int debounce = 350, const boolean debug = false )

Définition à la ligne 12 du fichier Bouton.cpp.

### 5.2.2.3 Bouton : :∼Bouton ( )

Définition à la ligne 18 du fichier Bouton.cpp.

### 5.2.3 Documentation des fonctions membres

5.2.3.1 bool Bouton : :testBoitierFerme ( const volatile bool & interruptOuvBoi, const bool & boitierOuvert )

--—test boitier ferme---—

Définition à la ligne 66 du fichier Bouton.cpp.

Voici le graphe des appelants de cette fonction :

Bouton::testBoitierFerme | routineTestFermetureBoitier | loop

5.2.3.2 bool Bouton : :testBoitierOuvert ( const volatile bool & interruptOuvBoi, const bool & boitierOuvert )

--—test boitier ouvert---—

Définition à la ligne 57 du fichier Bouton.cpp.

Voici le graphe des appelants de cette fonction :

Bouton::testBoitierOuvert | routineTestOuvertureBoitier | loop | Généré par Doxygen

5.2 Référence de la classe Bouton | 17

### 5.2.3.3 void Bouton : :testInterruptionBoitier ( volatile bool & interruptOuvBoi )

--—test IT ouverture boitier--—

Définition à la ligne 50 du fichier Bouton.cpp.

Voici le graphe des appelants de cette fonction :

Bouton::testInterruption
Boitier | myInterruptINT1 | setup

### 5.2.3.4 void Bouton : :testInterruptionBp ( volatile bool & interruptBp )

--—test IT Bp--—

Définition à la ligne 42 du fichier Bouton.cpp.

Voici le graphe des appelants de cette fonction :

Bouton::testInterruptionBp | myInterruptINT1 | setup

### 5.2.3.5 void Bouton : :testRelacheBp ( volatile bool & interruptBp )

--—test relache Bp--—

Définition à la ligne 33 du fichier Bouton.cpp.

Voici le graphe des appelants de cette fonction :

Bouton::testRelacheBp | routineInterruptionBp | loop Généré par Doxygen

### 18 Documentation des classes

### 5.2.3.6 bool Bouton : :testToucheBp ( )

--—test touche Bp--—

Définition à la ligne 23 du fichier Bouton.cpp.

Voici le graphe des appelants de cette fonction :

Bouton::testToucheBp | routineInterruptionBp | loop

### 5.2.4 Documentation des données membres

### 5.2.4.1 const int Bouton : :m_debounce [protected]

Définition à la ligne 30 du fichier Bouton.h.

### 5.2.4.2 const boolean Bouton : :m_debug [protected]

Définition à la ligne 27 du fichier Bouton.h.

### 5.2.4.3 const byte Bouton : :m_pinBoitier [protected]

Définition à la ligne 29 du fichier Bouton.h.

### 5.2.4.4 const byte Bouton : :m_pinBp [protected]

Définition à la ligne 28 du fichier Bouton.h.

### 5.2.4.5 bool Bouton : :m_relacheBp [protected]

Définition à la ligne 32 du fichier Bouton.h.

### 5.2.4.6 int Bouton : :m_tempoDebounce [protected]

Définition à la ligne 31 du fichier Bouton.h.

La documentation de cette classe a été générée à partir des fichiers suivants :
— /home/jlm-atelier/Bureau/GIT/Porte-poulailler-automatique/porte_poulailler_affichage_clavier_rtc/Bouton.←-
h
— /home/jlm-atelier/Bureau/GIT/Porte-poulailler-automatique/porte_poulailler_affichage_clavier_rtc/Bouton.←-
cpp

5.3 Référence de la classe Clavier | 19

### 5.3 Référence de la classe Clavier

#include <Clavier.h>

Graphe d'héritage de Clavier :

Clavier
# m_debug

# m_oldKey

# m_NumKeys

# m_MenuManuel

# m_AdcKeyVal

+ Clavier()
+ Clavier()
+ ~Clavier()
+ get_key()
+ read_key()
+ positionMenu()
+ deplacementDansMenu()
+ relacheTouche()
+ testTouche5()

Bouton
# m_debug

# m_pinBp

# m_pinBoitier

# m_debounce

# m_tempoDebounce

# m_relacheBp

+ Bouton()
+ Bouton()
+ ~Bouton()
+ testToucheBp()
+ testRelacheBp()
+ testInterruptionBp()
+ testInterruptionBoitier() + testBoitierOuvert()
+ testBoitierFerme()

### 20 Documentation des classes

Graphe de collaboration de Clavier :

Clavier
# m_debug

# m_oldKey

# m_NumKeys

# m_MenuManuel

# m_AdcKeyVal

+ Clavier()
+ Clavier()
+ ~Clavier()
+ get_key()
+ read_key()
+ positionMenu()
+ deplacementDansMenu()
+ relacheTouche()
+ testTouche5()

Bouton
# m_debug

# m_pinBp

# m_pinBoitier

# m_debounce

# m_tempoDebounce

# m_relacheBp

+ Bouton()
+ Bouton()
+ ~Bouton()
+ testToucheBp()
+ testRelacheBp()
+ testInterruptionBp()
+ testInterruptionBoitier() + testBoitierOuvert()
+ testBoitierFerme()

Fonctions membres publiques

— Clavier ()
— Clavier (byte nbMenu, const byte pinBp, const byte pinBoitier, const int debounce=350, const boolean debug=false)
— ∼Clavier ()
— int get_key (int &input)

---—routine get_key : Convert ADC value to key number---—
— int read_key (const int &sensor)

--—routine read_key : lecture du clavier--—
— void positionMenu (byte &positionMenu, const byte &toucheClavier)

--—position du menu pour l'affichage - touches 2 et 3 --—

5.3 Référence de la classe Clavier | 21

— bool deplacementDansMenu (const &touche, bool &relache, const bool &reglage)

--—deplacement dans le menu--—
— void relacheTouche (const int &touche, bool &relache)

--—relache touche--—
— bool testTouche5 (const &touche, bool &relache)

--—test touche 5--—

Attributs protégés
— const boolean m_debug
— const byte m_oldKey
— const byte m_NumKeys
— byte m_MenuManuel
— int m_AdcKeyVal [5]

### 5.3.1 Description détaillée

Clavier.h (p. ??) prototype de la classe Clavier (p. ??) Définition à la ligne 11 du fichier Clavier.h.

### 5.3.2 Documentation des constructeurs et destructeur

### 5.3.2.1 Clavier : :Clavier ( )

Clavier.cpp (p. ??) définitions de la classe Clavier (p. ??)
Définition à la ligne 7 du fichier Clavier.cpp.

5.3.2.2 Clavier : :Clavier ( byte nbMenu, const byte pinBp, const byte pinBoitier, const int debounce = 350, const boolean debug = false )

Définition à la ligne 13 du fichier Clavier.cpp.

### 5.3.2.3 Clavier : :∼Clavier ( )

Définition à la ligne 20 du fichier Clavier.cpp.

### 5.3.3 Documentation des fonctions membres

5.3.3.1 bool Clavier : :deplacementDansMenu ( const & touche, bool & relache, const bool & reglage )

--—deplacement dans le menu--—
Définition à la ligne 79 du fichier Clavier.cpp.
Voici le graphe des appelants de cette fonction :
Clavier::deplacementDansMenu | lectureClavier | loop Généré par Doxygen

### 22 Documentation des classes

### 5.3.3.2 int Clavier : :get_key ( int & input )

---—routine get_key : Convert ADC value to key number---—

Définition à la ligne 25 du fichier Clavier.cpp.

Voici le graphe des appelants de cette fonction :

Clavier::get_key | Clavier::read_key | lectureClavier | loop

### 5.3.3.3 void Clavier : :positionMenu ( byte & positionMenu, const byte & toucheClavier )

--—position du menu pour l'affichage - touches 2 et 3 --—

Définition à la ligne 54 du fichier Clavier.cpp.

Voici le graphe des appelants de cette fonction :

Clavier::positionMenu | lectureClavier | loop

### 5.3.3.4 int Clavier : :read_key ( const int & sensor )

--—routine read_key : lecture du clavier--—

Définition à la ligne 39 du fichier Clavier.cpp.

Voici le graphe d'appel pour cette fonction :

Clavier::read_key | Clavier::get_key | Généré par Doxygen

5.3 Référence de la classe Clavier | 23

Voici le graphe des appelants de cette fonction :

Clavier::read_key | lectureClavier | loop

### 5.3.3.5 void Clavier : :relacheTouche ( const int & touche, bool & relache )

--—relache touche--—

Définition à la ligne 72 du fichier Clavier.cpp.

Voici le graphe des appelants de cette fonction :

Clavier::relacheTouche | lectureClavier | loop

### 5.3.3.6 bool Clavier : :testTouche5 ( const & touche, bool & relache )

--—test touche 5--—

Définition à la ligne 89 du fichier Clavier.cpp.

Voici le graphe des appelants de cette fonction :

Clavier::testTouche5 | eclairageAfficheur | loop

### 5.3.4 Documentation des données membres

### 5.3.4.1 int Clavier : :m_AdcKeyVal[5] [protected]

Définition à la ligne 33 du fichier Clavier.h.

### 24 Documentation des classes

### 5.3.4.2 const boolean Clavier : :m_debug [protected]

Définition à la ligne 29 du fichier Clavier.h.

### 5.3.4.3 byte Clavier : :m_MenuManuel [protected]

Définition à la ligne 32 du fichier Clavier.h.

### 5.3.4.4 const byte Clavier : :m_NumKeys [protected]

Définition à la ligne 31 du fichier Clavier.h.

### 5.3.4.5 const byte Clavier : :m_oldKey [protected]

Définition à la ligne 30 du fichier Clavier.h.
La documentation de cette classe a été générée à partir des fichiers suivants : — /home/jlm-atelier/Bureau/GIT/Porte-poulailler-automatique/porte_poulailler_affichage_clavier_rtc/Clavier.h — /home/jlm-atelier/Bureau/GIT/Porte-poulailler-automatique/porte_poulailler_affichage_clavier_rtc/Clavier.←-
cpp

### 5.4 Référence de la classe Codeur

#include <Codeur.h>

Graphe de collaboration de Codeur :

Codeur
# m_roueCodeusePin

# m_finDeCourseMax

# m_debug

# m_compteRoueCodeuse

# m_interruptRoueCodeuse

# m_positionRoueCodeuse

# m_finDeCourseFermeture

# m_finDeCourseOuverture

+ Codeur()
+ ~Codeur()
+ init()
+ testCompteurRoueCodeuse() + reglageFinDeCourse()
+ compteurRoueCodeuse()
+ get_m_compteRoueCodeuse() + set_m_compteRoueCodeuse() + get_m_finDeCourseFermeture()
+ set_m_finDeCourseFermeture()
+ get_m_finDeCourseOuverture()
+ set_m_finDeCourseOuverture() | Généré par Doxygen

5.4 Référence de la classe Codeur | 25

Fonctions membres publiques

— Codeur (const byte roueCodeusePin, unsigned int finDeCourseFermeture=250, unsigned int finDe←-
CourseOuverture=150, unsigned int compteRoueCodeuse=150, boolean debug=false)
— ∼Codeur ()
— void init ()

--—initialisation--—
— byte testCompteurRoueCodeuse (byte tolerance)

--—test du compteur roue codeuse pour affichage ouvert ou ferme--—
— unsigned int reglageFinDeCourse (bool ouvFerm, byte touche)

--—reglage de la fin de course--—
— void compteurRoueCodeuse (bool ouvFerm)

--—compteur roue codeuse--—
— unsigned int get_m_compteRoueCodeuse ()
— void set_m_compteRoueCodeuse (unsigned int compteRoueCodeuse) — unsigned int get_m_finDeCourseFermeture ()
— void set_m_finDeCourseFermeture (unsigned int finDeCourseFermeture) — unsigned int get_m_finDeCourseOuverture ()
— void set_m_finDeCourseOuverture (unsigned int finDeCourseOuverture)

Attributs protégés

— const byte m_roueCodeusePin
— const unsigned int m_finDeCourseMax
— const boolean m_debug
— volatile unsigned int m_compteRoueCodeuse
— volatile boolean m_interruptRoueCodeuse — volatile boolean m_positionRoueCodeuse — unsigned int m_finDeCourseFermeture
— unsigned int m_finDeCourseOuverture

### 5.4.1 Description détaillée

Codeur.h (p. ??) prototype de la classe Codeur (p. ??) codeur optique de 20 pas

Définition à la ligne 11 du fichier Codeur.h.

### 5.4.2 Documentation des constructeurs et destructeur

5.4.2.1 Codeur : :Codeur ( const byte roueCodeusePin, unsigned int finDeCourseFermeture = 250, unsigned int finDeCourseOuverture = 150, unsigned int compteRoueCodeuse = 150, boolean debug = false )

Codeur.cpp (p. ??) définitions de la classe Codeur (p. ??) Codeur (p. ??) optqie de 20 pas

Définition à la ligne 9 du fichier Codeur.cpp.

### 5.4.2.2 Codeur : :∼Codeur ( )

Définition à la ligne 15 du fichier Codeur.cpp.

### 26 Documentation des classes

### 5.4.3 Documentation des fonctions membres

### 5.4.3.1 void Codeur : :compteurRoueCodeuse ( bool ouvFerm )

--—compteur roue codeuse--—
Définition à la ligne 63 du fichier Codeur.cpp.
Voici le graphe des appelants de cette fonction :
Codeur::compteurRoueCodeuse | fermeturePorte | loop

### 5.4.3.2 unsigned int Codeur : :get_m_compteRoueCodeuse ( )

Définition à la ligne 81 du fichier Codeur.cpp.
Voici le graphe des appelants de cette fonction :

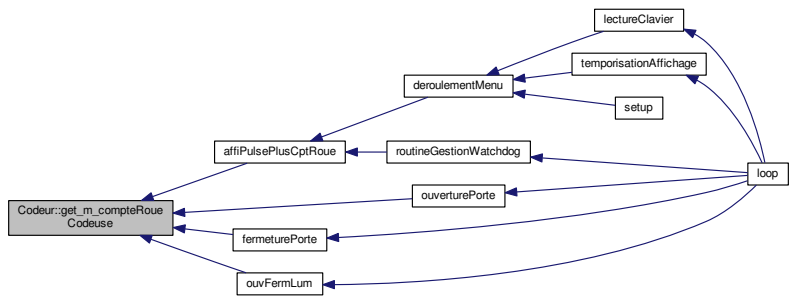
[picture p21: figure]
Codeur::get_m_compteRoue Codeuse; affiPulsePlusCptRoue; ouverturePorte; fermeturePorte; ouvFermLum; deroulementMenu; routineGestionWatchdog; lectureClavier; temporisationAffichage; setup; loop

### 5.4.3.3 unsigned int Codeur : :get_m_finDeCourseFermeture ( )

Définition à la ligne 90 du fichier Codeur.cpp.
Voici le graphe des appelants de cette fonction :

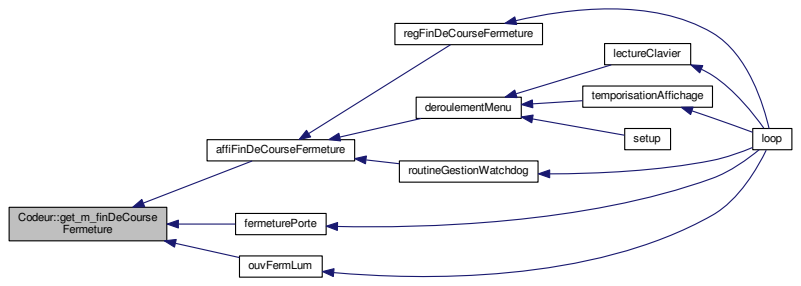
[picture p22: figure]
Codeur::get_m_finDeCourse Fermeture; affiFinDeCourseFermeture; fermeturePorte; ouvFermLum; regFinDeCourseFermeture; deroulementMenu; routineGestionWatchdog; loop; lectureClavier; temporisationAffichage; setup

5.4 Référence de la classe Codeur | 27

### 5.4.3.4 unsigned int Codeur : :get_m_finDeCourseOuverture ( )

Définition à la ligne 99 du fichier Codeur.cpp.
Voici le graphe des appelants de cette fonction :

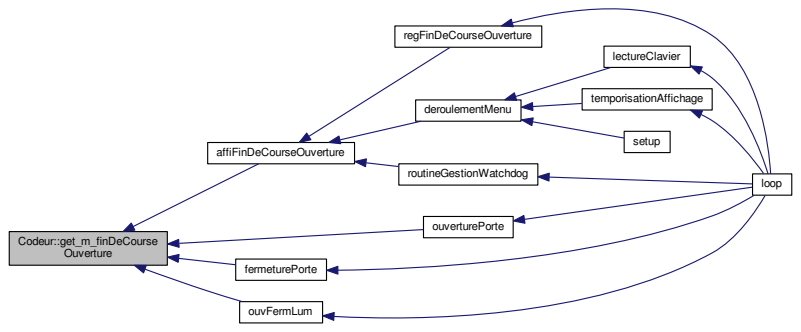
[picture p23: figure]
Codeur::get_m_finDeCourse Ouverture; affiFinDeCourseOuverture; ouverturePorte; fermeturePorte; ouvFermLum; regFinDeCourseOuverture; deroulementMenu; routineGestionWatchdog; loop; lectureClavier; temporisationAffichage; setup

### 5.4.3.5 void Codeur : :init ( )

--—initialisation--—
Définition à la ligne 20 du fichier Codeur.cpp. Voici le graphe des appelants de cette fonction :
Codeur::init | setup

### 5.4.3.6 unsigned int Codeur : :reglageFinDeCourse ( bool ouvFerm, byte touche )

--—reglage de la fin de course--—
Définition à la ligne 39 du fichier Codeur.cpp.
Voici le graphe des appelants de cette fonction :

Codeur::reglageFinDeCourse

regFinDeCourseFermeture

regFinDeCourseOuverture

loop

### 28 Documentation des classes

### 5.4.3.7 void Codeur : :set_m_compteRoueCodeuse ( unsigned int compteRoueCodeuse )

Définition à la ligne 85 du fichier Codeur.cpp.

Voici le graphe des appelants de cette fonction :

Codeur::set_m_compteRoue
Codeuse

ouverturePorte

fermeturePorte

loop

### 5.4.3.8 void Codeur : :set_m_finDeCourseFermeture ( unsigned int finDeCourseFermeture )

Définition à la ligne 94 du fichier Codeur.cpp.

Voici le graphe des appelants de cette fonction :

Codeur::set_m_finDeCourse
Fermeture | setup

### 5.4.3.9 void Codeur : :set_m_finDeCourseOuverture ( unsigned int finDeCourseOuverture )

Définition à la ligne 103 du fichier Codeur.cpp.

Voici le graphe des appelants de cette fonction :

Codeur::set_m_finDeCourse
Ouverture | setup

5.4 Référence de la classe Codeur | 29

### 5.4.3.10 byte Codeur : :testCompteurRoueCodeuse ( byte tolerance )

--—test du compteur roue codeuse pour affichage ouvert ou ferme--—

Définition à la ligne 26 du fichier Codeur.cpp.

Voici le graphe des appelants de cette fonction :

Codeur::testCompteurRoue
Codeuse | affiPulsePlusCptRoue

deroulementMenu

routineGestionWatchdog

lectureClavier

temporisationAffichage

setup

loop

### 5.4.4 Documentation des données membres

### 5.4.4.1 volatile unsigned int Codeur : :m_compteRoueCodeuse [protected]

Définition à la ligne 37 du fichier Codeur.h.

### 5.4.4.2 const boolean Codeur : :m_debug [protected]

Définition à la ligne 36 du fichier Codeur.h.

### 5.4.4.3 unsigned int Codeur : :m_finDeCourseFermeture [protected]

Définition à la ligne 40 du fichier Codeur.h.

### 5.4.4.4 const unsigned int Codeur : :m_finDeCourseMax [protected]

Définition à la ligne 35 du fichier Codeur.h.

### 5.4.4.5 unsigned int Codeur : :m_finDeCourseOuverture [protected]

Définition à la ligne 41 du fichier Codeur.h.

### 5.4.4.6 volatile boolean Codeur : :m_interruptRoueCodeuse [protected]

Définition à la ligne 38 du fichier Codeur.h.

### 30 Documentation des classes

### 5.4.4.7 volatile boolean Codeur : :m_positionRoueCodeuse [protected]

Définition à la ligne 39 du fichier Codeur.h.

### 5.4.4.8 const byte Codeur : :m_roueCodeusePin [protected]

Définition à la ligne 34 du fichier Codeur.h.
La documentation de cette classe a été générée à partir des fichiers suivants : — /home/jlm-atelier/Bureau/GIT/Porte-poulailler-automatique/porte_poulailler_affichage_clavier_rtc/Codeur.←-

h
— /home/jlm-atelier/Bureau/GIT/Porte-poulailler-automatique/porte_poulailler_affichage_clavier_rtc/Codeur.←-
cpp

### 5.5 Référence de la classe HorlogeDS3232

#include <HorlogeDS3232.h>

Graphe d'héritage de HorlogeDS3232 :

HorlogeDS3232
# m_debug

# m_deviceAddress

# m_rtcINT

# m_alarm1Hour

# m_alarm1Minute

# m_alarm1Second

# m_alarm2Hour

# m_alarm2Minute

+ HorlogeDS3232()
+ HorlogeDS3232()
+ ~HorlogeDS3232()
+ init()
+ testPresenceCarteRTC()
+ decToBcd()
+ bcdToDec()
+ i2c_eeprom_write_byte()
+ i2c_eeprom_read_byte()
+ lectureRegistreEtConversion() et 11 de plus...
# lectureHoraireALARM1()

# lectureHoraireALARM2()

DS3232RTC

5.5 Référence de la classe HorlogeDS3232 | 31

Graphe de collaboration de HorlogeDS3232 :

HorlogeDS3232
# m_debug

# m_deviceAddress

# m_rtcINT

# m_alarm1Hour

# m_alarm1Minute

# m_alarm1Second

# m_alarm2Hour

# m_alarm2Minute

+ HorlogeDS3232()
+ HorlogeDS3232()
+ ~HorlogeDS3232()
+ init()
+ testPresenceCarteRTC()
+ decToBcd()
+ bcdToDec()
+ i2c_eeprom_write_byte()
+ i2c_eeprom_read_byte()
+ lectureRegistreEtConversion() et 11 de plus...
# lectureHoraireALARM1()

# lectureHoraireALARM2()

DS3232RTC

Fonctions membres publiques

— HorlogeDS3232 ()
— HorlogeDS3232 (const byte adresseMemoireI2C=0x57, const byte m_rtcINT=5, const boolean debug=false)
— ∼HorlogeDS3232 ()
— void init ()

--—initialisation--—
— bool testPresenceCarteRTC ()

--—verification de la presence de la carte RTC / memoire 24C32--—
— byte decToBcd (byte val)

--—routine decToBcd : Convert normal decimal numbers to binary coded decimal--—
— byte bcdToDec (byte val)

--—routine bcdToDec : Convert binary coded decimal to normal decimal numbers--—
— void i2c_eeprom_write_byte (unsigned int eeaddress, byte data)

--—ecriture dans l'eeprom at24c32 de la carte rtc---—
— byte i2c_eeprom_read_byte (unsigned int eeaddress)

--—lecture de l'eeprom at24c32 de la carte rtc---—
— byte lectureRegistreEtConversion (byte adresse, byte operationAND=0xFF)

---—lecture registre et conversion--—

### 32 Documentation des classes

— byte reglageHeure (const byte touche, byte tmDateTime, const byte type)

--—reglaged date time--—
— void testInterruptRTC (volatile bool &interruptRTC)

--—test IT RTC--—
— void reglageAlarme (const byte touche, const byte alarme, const byte type)

--—reglage de l'alarme--—
— void sauvEepromChoix (unsigned int valeurChoix, const bool matinSoirOuvFerm, const bool lumiereFin←-DeCourse)

--—sauvegarde dans l'eeprom I2C le choix de la lumiere ou de la valeur de fin de course--—
— float calculTemperature (const bool typeTemperature)

---—valeur de la temperature en fonction du type---—
— bool choixTypeOuvertureFermeture (bool choixOuvertureFermeture, const byte alarme)

--—mise à jour du choix du type d'ouverture / fermeture--—
— byte get_m_alarm1Hour ()
— byte get_m_alarm1Minute ()
— byte get_m_alarm1Second ()
— byte get_m_alarm2Hour () — byte get_m_alarm2Minute ()

Fonctions membres protégées

— void lectureHoraireALARM1 ()

--—lecture horaire ALARM1--— — void lectureHoraireALARM2 ()

--—lecture horaire ALARM2--—

Attributs protégés

— const boolean m_debug
— const int m_deviceAddress
— const byte m_rtcINT
— byte m_alarm1Hour
— byte m_alarm1Minute
— byte m_alarm1Second
— byte m_alarm2Hour
— byte m_alarm2Minute

### 5.5.1 Description détaillée

Définition à la ligne 15 du fichier HorlogeDS3232.h.

### 5.5.2 Documentation des constructeurs et destructeur

### 5.5.2.1 HorlogeDS3232 : :HorlogeDS3232 ( )

Définition à la ligne 8 du fichier HorlogeDS3232.cpp.

5.5.2.2 HorlogeDS3232 : :HorlogeDS3232 ( const byte adresseMemoireI2C = 0x57, const byte m_rtcINT = 5, const boolean debug = false )

Définition à la ligne 15 du fichier HorlogeDS3232.cpp.

5.5 Référence de la classe HorlogeDS3232 | 33

### 5.5.2.3 HorlogeDS3232 : :∼HorlogeDS3232 ( )

Définition à la ligne 22 du fichier HorlogeDS3232.cpp.

### 5.5.3 Documentation des fonctions membres

### 5.5.3.1 byte HorlogeDS3232 : :bcdToDec ( byte val )

--—routine bcdToDec : Convert binary coded decimal to normal decimal numbers--—

Définition à la ligne 57 du fichier HorlogeDS3232.cpp.

Voici le graphe des appelants de cette fonction :

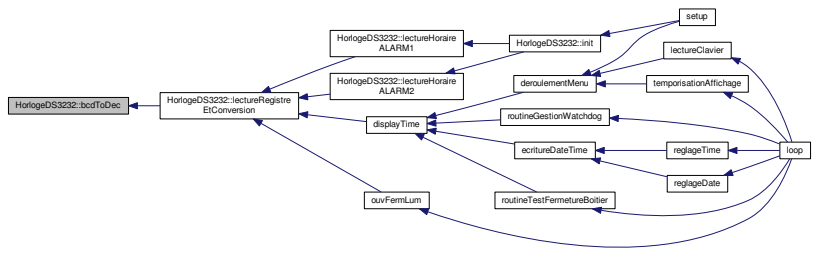
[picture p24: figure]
HorlogeDS3232::bcdToDec; HorlogeDS3232::lectureRegistre; EtConversion; HorlogeDS3232::lectureHoraire ALARM1; HorlogeDS3232::lectureHoraire ALARM2; displayTime; ouvFermLum; HorlogeDS3232::init; setup; ecritureDateTime; routineTestFermetureBoitier; deroulementMenu; routineGestionWatchdog; reglageDate; reglageTime; loop; lectureClavier; temporisationAffichage

### 5.5.3.2 float HorlogeDS3232 : :calculTemperature ( const bool typeTemperature )

---—valeur de la temperature en fonction du type---—

Définition à la ligne 183 du fichier HorlogeDS3232.cpp.

Voici le graphe des appelants de cette fonction :

HorlogeDS3232::calculTemperature | read_temp

deroulementMenu

routineGestionWatchdog

lectureClavier

temporisationAffichage

setup

loop

### 34 Documentation des classes

5.5.3.3 bool HorlogeDS3232 : :choixTypeOuvertureFermeture ( bool choixOuvertureFermeture, const byte alarme )

--—mise à jour du choix du type d'ouverture / fermeture--—

Définition à la ligne 195 du fichier HorlogeDS3232.cpp.

Voici le graphe d'appel pour cette fonction :

HorlogeDS3232::choixType
OuvertureFermeture

HorlogeDS3232::i2c
_eeprom_write_byte

Voici le graphe des appelants de cette fonction :

HorlogeDS3232::choixType
OuvertureFermeture | choixOuvFerm | loop

### 5.5.3.4 byte HorlogeDS3232 : :decToBcd ( byte val )

--—routine decToBcd : Convert normal decimal numbers to binary coded decimal--—

Définition à la ligne 52 du fichier HorlogeDS3232.cpp.

### 5.5.3.5 byte HorlogeDS3232 : :get_m_alarm1Hour ( )

Définition à la ligne 205 du fichier HorlogeDS3232.cpp.

Voici le graphe des appelants de cette fonction :

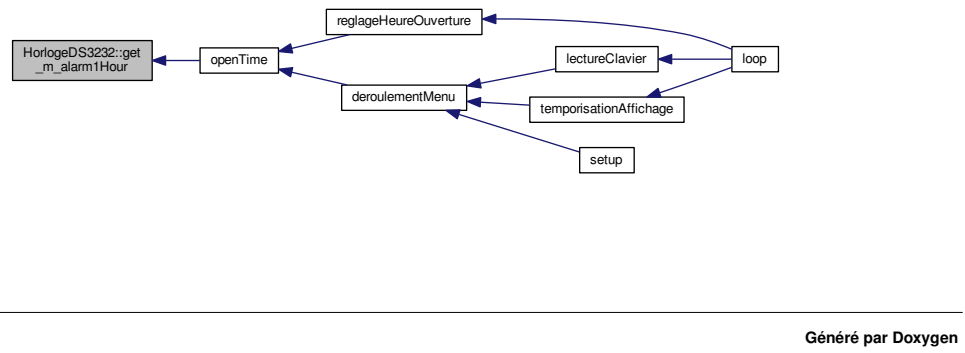
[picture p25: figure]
HorlogeDS3232::get; _m_alarm1Hour; openTime; reglageHeureOuverture; deroulementMenu; lectureClavier; loop; temporisationAffichage; setup; Généré par Doxygen

5.5 Référence de la classe HorlogeDS3232 | 35

### 5.5.3.6 byte HorlogeDS3232 : :get_m_alarm1Minute ( )

Définition à la ligne 210 du fichier HorlogeDS3232.cpp.

Voici le graphe des appelants de cette fonction :

### 5.5.3.7 byte HorlogeDS3232 : :get_m_alarm1Second ( )

Définition à la ligne 215 du fichier HorlogeDS3232.cpp.

Voici le graphe des appelants de cette fonction :

### 5.5.3.8 byte HorlogeDS3232 : :get_m_alarm2Hour ( )

Définition à la ligne 220 du fichier HorlogeDS3232.cpp.

Voici le graphe des appelants de cette fonction :

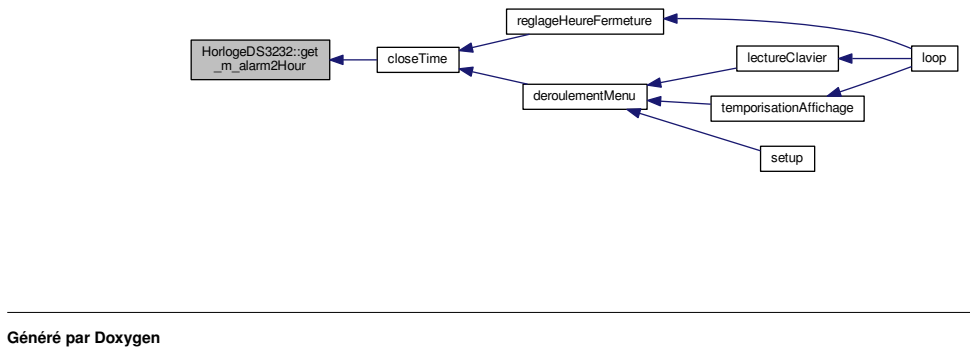
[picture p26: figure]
HorlogeDS3232::get; _m_alarm2Hour; closeTime; reglageHeureFermeture; deroulementMenu; lectureClavier; loop; temporisationAffichage; setup Généré par Doxygen

### 36 Documentation des classes

### 5.5.3.9 byte HorlogeDS3232 : :get_m_alarm2Minute ( )

Définition à la ligne 225 du fichier HorlogeDS3232.cpp.
Voici le graphe des appelants de cette fonction :

### 5.5.3.10 byte HorlogeDS3232 : :i2c_eeprom_read_byte ( unsigned int eeaddress )

--—lecture de l'eeprom at24c32 de la carte rtc---—
Définition à la ligne 73 du fichier HorlogeDS3232.cpp.
Voici le graphe des appelants de cette fonction :

HorlogeDS3232::i2c
_eeprom_read_byte | setup

5.5.3.11 void HorlogeDS3232 : :i2c_eeprom_write_byte ( unsigned int eeaddress, byte data )

--—ecriture dans l'eeprom at24c32 de la carte rtc---—
Définition à la ligne 63 du fichier HorlogeDS3232.cpp.
Voici le graphe des appelants de cette fonction :

HorlogeDS3232::i2c _eeprom_write_byte; HorlogeDS3232::sauvEeprom Choix; HorlogeDS3232::choixType OuvertureFermeture; choixLumMatin; choixLumSoir; regFinDeCourseFermeture; regFinDeCourseOuverture; loop; choixOuvFerm; Généré par Doxygen

5.5 Référence de la classe HorlogeDS3232 | 37

### 5.5.3.12 void HorlogeDS3232 : :init ( )

--—initialisation--—

Définition à la ligne 27 du fichier HorlogeDS3232.cpp.

Voici le graphe d'appel pour cette fonction :

HorlogeDS3232::init

HorlogeDS3232::lectureHoraire ALARM1

HorlogeDS3232::lectureHoraire ALARM2

HorlogeDS3232::lectureRegistre
EtConversion | HorlogeDS3232::bcdToDec

Voici le graphe des appelants de cette fonction :

HorlogeDS3232::init | setup

### 5.5.3.13 void HorlogeDS3232 : :lectureHoraireALARM1 ( ) [protected]

--—lecture horaire ALARM1--—

Définition à la ligne 125 du fichier HorlogeDS3232.cpp.

Voici le graphe d'appel pour cette fonction :

HorlogeDS3232::lectureHoraire ALARM1

HorlogeDS3232::lectureRegistre
EtConversion | HorlogeDS3232::bcdToDec

Voici le graphe des appelants de cette fonction :

HorlogeDS3232::lectureHoraire
ALARM1 | HorlogeDS3232::init | setup

### 38 Documentation des classes

### 5.5.3.14 void HorlogeDS3232 : :lectureHoraireALARM2 ( ) [protected]

--—lecture horaire ALARM2--—

Définition à la ligne 132 du fichier HorlogeDS3232.cpp.

Voici le graphe d'appel pour cette fonction :

HorlogeDS3232::lectureHoraire ALARM2

HorlogeDS3232::lectureRegistre
EtConversion | HorlogeDS3232::bcdToDec

Voici le graphe des appelants de cette fonction :

HorlogeDS3232::lectureHoraire
ALARM2 | HorlogeDS3232::init | setup

5.5.3.15 byte HorlogeDS3232 : :lectureRegistreEtConversion ( byte adresse, byte operationAND = 0xFF )

---—lecture registre et conversion--—

Définition à la ligne 85 du fichier HorlogeDS3232.cpp.

Voici le graphe d'appel pour cette fonction :

HorlogeDS3232::lectureRegistre
EtConversion | HorlogeDS3232::bcdToDec

5.5 Référence de la classe HorlogeDS3232 | 39

Voici le graphe des appelants de cette fonction :

HorlogeDS3232::lectureRegistre EtConversion; HorlogeDS3232::lectureHoraire ALARM1; HorlogeDS3232::lectureHoraire ALARM2; displayTime; ouvFermLum; HorlogeDS3232::init; setup; ecritureDateTime; routineTestFermetureBoitier; deroulementMenu; routineGestionWatchdog; reglageDate; reglageTime; loop; lectureClavier; temporisationAffichage

5.5.3.16 void HorlogeDS3232 : :reglageAlarme ( const byte touche, const byte alarme, const byte type )

--—reglage de l'alarme--—

Définition à la ligne 138 du fichier HorlogeDS3232.cpp.

Voici le graphe d'appel pour cette fonction :

HorlogeDS3232::reglageAlarme | HorlogeDS3232::reglageHeure

Voici le graphe des appelants de cette fonction :

HorlogeDS3232::reglageAlarme

reglageHeureFermeture

reglageHeureOuverture

loop

5.5.3.17 byte HorlogeDS3232 : :reglageHeure ( const byte touche, byte tmDateTime, const byte type )

--—reglaged date time--—

Définition à la ligne 90 du fichier HorlogeDS3232.cpp.

### 40 Documentation des classes

Voici le graphe des appelants de cette fonction :

HorlogeDS3232::reglageHeure; HorlogeDS3232::reglageAlarme; reglageDate; reglageTime; reglageHeureFermeture; reglageHeureOuverture; loop

5.5.3.18 void HorlogeDS3232 : :sauvEepromChoix ( unsigned int valeurChoix, const bool matinSoirOuvFerm, const bool lumiereFinDeCourse )

--—sauvegarde dans l'eeprom I2C le choix de la lumiere ou de la valeur de fin de course--—

Définition à la ligne 167 du fichier HorlogeDS3232.cpp.

Voici le graphe d'appel pour cette fonction :

HorlogeDS3232::sauvEeprom
Choix

HorlogeDS3232::i2c
_eeprom_write_byte

Voici le graphe des appelants de cette fonction :

HorlogeDS3232::sauvEeprom Choix; choixLumMatin; choixLumSoir; regFinDeCourseFermeture; regFinDeCourseOuverture; loop

5.5 Référence de la classe HorlogeDS3232 | 41

### 5.5.3.19 void HorlogeDS3232 : :testInterruptRTC ( volatile bool & interruptRTC )

--—test IT RTC--—

Définition à la ligne 45 du fichier HorlogeDS3232.cpp.

Voici le graphe des appelants de cette fonction :

HorlogeDS3232::testInterruptRTC | myInterruptINT1 | setup

### 5.5.3.20 bool HorlogeDS3232 : :testPresenceCarteRTC ( )

--—verification de la presence de la carte RTC / memoire 24C32--—

Définition à la ligne 35 du fichier HorlogeDS3232.cpp.

Voici le graphe des appelants de cette fonction :

HorlogeDS3232::testPresence
CarteRTC | setup

### 5.5.4 Documentation des données membres

### 5.5.4.1 byte HorlogeDS3232 : :m_alarm1Hour [protected]

Définition à la ligne 55 du fichier HorlogeDS3232.h.

### 5.5.4.2 byte HorlogeDS3232 : :m_alarm1Minute [protected]

Définition à la ligne 56 du fichier HorlogeDS3232.h.

### 5.5.4.3 byte HorlogeDS3232 : :m_alarm1Second [protected]

Définition à la ligne 57 du fichier HorlogeDS3232.h.

### 42 Documentation des classes

### 5.5.4.4 byte HorlogeDS3232 : :m_alarm2Hour [protected]

Définition à la ligne 58 du fichier HorlogeDS3232.h.

### 5.5.4.5 byte HorlogeDS3232 : :m_alarm2Minute [protected]

Définition à la ligne 59 du fichier HorlogeDS3232.h.

### 5.5.4.6 const boolean HorlogeDS3232 : :m_debug [protected]

Définition à la ligne 52 du fichier HorlogeDS3232.h.

### 5.5.4.7 const int HorlogeDS3232 : :m_deviceAddress [protected]

Définition à la ligne 53 du fichier HorlogeDS3232.h.

### 5.5.4.8 const byte HorlogeDS3232 : :m_rtcINT [protected]

Définition à la ligne 54 du fichier HorlogeDS3232.h.

La documentation de cette classe a été générée à partir des fichiers suivants :

— /home/jlm-atelier/Bureau/GIT/Porte-poulailler-automatique/porte_poulailler_affichage_clavier_rtc/Horloge←-
DS3232.h
— /home/jlm-atelier/Bureau/GIT/Porte-poulailler-automatique/porte_poulailler_affichage_clavier_rtc/Horloge←-
DS3232.cpp

### 5.6 Référence de la classe LcdDigoleI2C

#include <LcdDigoleI2C.h>

5.6 Référence de la classe LcdDigoleI2C | 43

Graphe d'héritage de LcdDigoleI2C :

LcdDigoleI2C
# m_debug

# m_taille

# m_decalage

# m_ligne

# m_deplacement

# m_retroEclairage

+ LcdDigoleI2C()
+ ~LcdDigoleI2C()
+ init()
+ effacementAfficheur()
+ affichageUneLigne()
+ resetPos()
+ affichageDateHeure()
+ transformation()
+ affichageLumFinCourse()
+ affichageVoltage()
et 11 de plus...

DigoleSerialDisp

### 44 Documentation des classes

Graphe de collaboration de LcdDigoleI2C :

LcdDigoleI2C
# m_debug

# m_taille

# m_decalage

# m_ligne

# m_deplacement

# m_retroEclairage

+ LcdDigoleI2C()
+ ~LcdDigoleI2C()
+ init()
+ effacementAfficheur()
+ affichageUneLigne()
+ resetPos()
+ affichageDateHeure()
+ transformation()
+ affichageLumFinCourse()
+ affichageVoltage()
et 11 de plus...

DigoleSerialDisp

Fonctions membres publiques

— LcdDigoleI2C (TwoWire ∗, char, byte taille, boolean debug=false)
— ∼LcdDigoleI2C ()
— void init ()

--—initialisation for text LCD adapter--—
— void effacementAfficheur ()

--—effacement de l'afficheur-—
— void affichageUneLigne (String chaine)

-—affichage une ligne--—
— void resetPos (byte ligne)

--—reset display position and clean the line--—
— void affichageDateHeure (String jourSemaine, byte jourHeure, byte moisMinute, byte anneeSeconde)

--—affichage de la date ou de l'heure--—
— String transformation (String chaine, byte dateHeure)

--—transformation donnees date et heure---—
— void affichageLumFinCourse (unsigned int lum, byte ligne, bool siNonReglable=0)

--—affichage lumiere et fin de course--—
— void affichageVoltage (float voltage, String texte, byte ligne)

--—affichage tensions--—
— void affichageChoix (bool ouverture, bool fermeture, byte ligne)

--—affichage choix ouverture fermeture--—
— void affichageServo (int pulse, int compteRoueCodeuse, byte ligne)

5.6 Référence de la classe LcdDigoleI2C | 45

--—affichage pulse et roue codeuse du servo----—
— void razLcd ()

--—remise à zero du lcd--—
— void bonjour (String chaine1, String chaine2)

--—affichage au demarrage sur les deux lignes--—
— void cursorPosition (byte decalage, byte ligne, char ∗texte)

--—position du curseur : decalage, ligne, texte--—
— void gestionCurseur (bool curseur)

---—activation / desactivation du curseur--—
— void retroEclairage ()

--—activation / desactivation du retro eclairage---—
— void choixRetroEclairage (bool choix)

--—choix activation / desactivation du retro eclairage---—
— void cursorPositionReglages (const byte &touche, bool &relache, bool &reglage, const byte decalageSup, const byte deplacement, const byte decalageInf)

--—position du cuseur pendant les reglages--—
— byte get_m_decalage ()
— void set_m_decalage (byte decalage)

Attributs protégés
— const boolean m_debug
— int const m_taille
— byte m_decalage
— byte m_ligne
— byte m_deplacement
— bool m_retroEclairage

### 5.6.1 Description détaillée

Définition à la ligne 25 du fichier LcdDigoleI2C.h.

### 5.6.2 Documentation des constructeurs et destructeur

5.6.2.1 LcdDigoleI2C : :LcdDigoleI2C ( TwoWire ∗ , char , byte taille, boolean debug = false )

Définition à la ligne 11 du fichier LcdDigoleI2C.cpp.

### 5.6.2.2 LcdDigoleI2C : :∼LcdDigoleI2C ( )

Définition à la ligne 16 du fichier LcdDigoleI2C.cpp.

### 5.6.3 Documentation des fonctions membres

5.6.3.1 void LcdDigoleI2C : :affichageChoix ( bool ouverture, bool fermeture, byte ligne )

--—affichage choix ouverture fermeture--—
Définition à la ligne 154 du fichier LcdDigoleI2C.cpp.
Voici le graphe d'appel pour cette fonction :
LcdDigoleI2C::affichageChoix | LcdDigoleI2C::affichageUne Ligne

LcdDigoleI2C::resetPos

LcdDigoleI2C::cursorPosition Généré par Doxygen

### 46 Documentation des classes

5.6.3.2 void LcdDigoleI2C : :affichageDateHeure ( String jourSemaine, byte jourHeure, byte moisMinute, byte anneeSeconde )

--—affichage de la date ou de l'heure--—

Définition à la ligne 91 du fichier LcdDigoleI2C.cpp.

Voici le graphe d'appel pour cette fonction :

LcdDigoleI2C::affichageDate Heure

LcdDigoleI2C::transformation

LcdDigoleI2C::affichageUne Ligne

LcdDigoleI2C::resetPos

LcdDigoleI2C::cursorPosition

5.6.3.3 void LcdDigoleI2C : :affichageLumFinCourse ( unsigned int lum, byte ligne, bool siNonReglable = 0 )

--—affichage lumiere et fin de course--—

Définition à la ligne 131 du fichier LcdDigoleI2C.cpp.

Voici le graphe d'appel pour cette fonction :

LcdDigoleI2C::affichageLum FinCourse

LcdDigoleI2C::affichageUne Ligne

LcdDigoleI2C::cursorPosition

LcdDigoleI2C::resetPos

5.6.3.4 void LcdDigoleI2C : :affichageServo ( int pulse, int compteRoueCodeuse, byte ligne )

--—affichage pulse et roue codeuse du servo----—

Définition à la ligne 166 du fichier LcdDigoleI2C.cpp.

Voici le graphe d'appel pour cette fonction :

LcdDigoleI2C::affichageServo

LcdDigoleI2C::affichageUne Ligne

LcdDigoleI2C::cursorPosition

LcdDigoleI2C::resetPos

5.6 Référence de la classe LcdDigoleI2C | 47

### 5.6.3.5 void LcdDigoleI2C : :affichageUneLigne ( String chaine )

-—affichage une ligne--—

Définition à la ligne 70 du fichier LcdDigoleI2C.cpp.

Voici le graphe d'appel pour cette fonction :

LcdDigoleI2C::affichageUne Ligne

LcdDigoleI2C::resetPos

LcdDigoleI2C::cursorPosition

Voici le graphe des appelants de cette fonction :

LcdDigoleI2C::affichageUne Ligne; LcdDigoleI2C::affichageDate Heure; LcdDigoleI2C::affichageLum FinCourse; LcdDigoleI2C::affichageVoltage; LcdDigoleI2C::affichageChoix; LcdDigoleI2C::affichageServo; LcdDigoleI2C::bonjour

### 5.6.3.6 void LcdDigoleI2C : :affichageVoltage ( float voltage, String texte, byte ligne )

--—affichage tensions--—

Définition à la ligne 142 du fichier LcdDigoleI2C.cpp.

### 48 Documentation des classes

Voici le graphe d'appel pour cette fonction :

LcdDigoleI2C::affichageVoltage

LcdDigoleI2C::affichageUne Ligne

LcdDigoleI2C::cursorPosition

LcdDigoleI2C::resetPos

### 5.6.3.7 void LcdDigoleI2C : :bonjour ( String chaine1, String chaine2 )

--—affichage au demarrage sur les deux lignes--—

Définition à la ligne 179 du fichier LcdDigoleI2C.cpp.

Voici le graphe d'appel pour cette fonction :

LcdDigoleI2C::bonjour; LcdDigoleI2C::gestionCurseur; LcdDigoleI2C::choixRetro Eclairage; LcdDigoleI2C::effacement Afficheur; LcdDigoleI2C::affichageUne Ligne; LcdDigoleI2C::cursorPosition; LcdDigoleI2C::resetPos

### 5.6.3.8 void LcdDigoleI2C : :choixRetroEclairage ( bool choix )

--—choix activation / desactivation du retro eclairage---—

Définition à la ligne 59 du fichier LcdDigoleI2C.cpp.

Voici le graphe des appelants de cette fonction :

LcdDigoleI2C::choixRetro
Eclairage | LcdDigoleI2C::bonjour

5.6 Référence de la classe LcdDigoleI2C | 49

### 5.6.3.9 void LcdDigoleI2C : :cursorPosition ( byte decalage, byte ligne, char ∗ texte )

--—position du curseur : decalage, ligne, texte--—

Définition à la ligne 202 du fichier LcdDigoleI2C.cpp.

Voici le graphe des appelants de cette fonction :

LcdDigoleI2C::cursorPosition; LcdDigoleI2C::affichageUne Ligne; LcdDigoleI2C::affichageLum FinCourse; LcdDigoleI2C::affichageVoltage; LcdDigoleI2C::affichageServo; LcdDigoleI2C::bonjour; LcdDigoleI2C::affichageDate Heure; LcdDigoleI2C::affichageChoix

5.6.3.10 void LcdDigoleI2C : :cursorPositionReglages ( const byte & touche, bool & relache, bool & reglage, const byte decalageSup, const byte deplacement, const byte decalageInf )

--—position du cuseur pendant les reglages--—

Définition à la ligne 208 du fichier LcdDigoleI2C.cpp.

### 5.6.3.11 void LcdDigoleI2C : :effacementAfficheur ( )

--—effacement de l'afficheur-—

Définition à la ligne 36 du fichier LcdDigoleI2C.cpp.

Voici le graphe des appelants de cette fonction :

LcdDigoleI2C::effacement
Afficheur

LcdDigoleI2C::init

LcdDigoleI2C::bonjour Généré par Doxygen

### 50 Documentation des classes

### 5.6.3.12 void LcdDigoleI2C : :gestionCurseur ( bool curseur )

---—activation / desactivation du curseur--—

Définition à la ligne 197 du fichier LcdDigoleI2C.cpp.

Voici le graphe des appelants de cette fonction :

LcdDigoleI2C::gestionCurseur | LcdDigoleI2C::bonjour

### 5.6.3.13 byte LcdDigoleI2C : :get_m_decalage ( )

Définition à la ligne 223 du fichier LcdDigoleI2C.cpp.

### 5.6.3.14 void LcdDigoleI2C : :init ( )

--—initialisation for text LCD adapter--—

Définition à la ligne 21 du fichier LcdDigoleI2C.cpp.

Voici le graphe d'appel pour cette fonction :

LcdDigoleI2C::init | LcdDigoleI2C::effacement Afficheur

### 5.6.3.15 void LcdDigoleI2C : :razLcd ( )

--—remise à zero du lcd--—

Définition à la ligne 41 du fichier LcdDigoleI2C.cpp.

5.6 Référence de la classe LcdDigoleI2C | 51

### 5.6.3.16 void LcdDigoleI2C : :resetPos ( byte ligne )

--—reset display position and clean the line--—

Définition à la ligne 79 du fichier LcdDigoleI2C.cpp.

Voici le graphe des appelants de cette fonction :

LcdDigoleI2C::resetPos; LcdDigoleI2C::affichageUne; Ligne; LcdDigoleI2C::affichageDate Heure; LcdDigoleI2C::affichageLum FinCourse; LcdDigoleI2C::affichageVoltage; LcdDigoleI2C::affichageChoix; LcdDigoleI2C::affichageServo; LcdDigoleI2C::bonjour

### 5.6.3.17 void LcdDigoleI2C : :retroEclairage ( )

--—activation / desactivation du retro eclairage---—

Définition à la ligne 48 du fichier LcdDigoleI2C.cpp.

### 5.6.3.18 void LcdDigoleI2C : :set_m_decalage ( byte decalage )

Définition à la ligne 228 du fichier LcdDigoleI2C.cpp.

### 5.6.3.19 String LcdDigoleI2C : :transformation ( String chaine, byte dateHeure )

--—transformation donnees date et heure---—

Définition à la ligne 113 du fichier LcdDigoleI2C.cpp.

Voici le graphe des appelants de cette fonction :

LcdDigoleI2C::transformation | LcdDigoleI2C::affichageDate
Heure Généré par Doxygen

### 52 Documentation des classes

### 5.6.4 Documentation des données membres

### 5.6.4.1 const boolean LcdDigoleI2C : :m_debug [protected]

Définition à la ligne 57 du fichier LcdDigoleI2C.h.

### 5.6.4.2 byte LcdDigoleI2C : :m_decalage [protected]

Définition à la ligne 59 du fichier LcdDigoleI2C.h.

### 5.6.4.3 byte LcdDigoleI2C : :m_deplacement [protected]

Définition à la ligne 61 du fichier LcdDigoleI2C.h.

### 5.6.4.4 byte LcdDigoleI2C : :m_ligne [protected]

Définition à la ligne 60 du fichier LcdDigoleI2C.h.

### 5.6.4.5 bool LcdDigoleI2C : :m_retroEclairage [protected]

Définition à la ligne 62 du fichier LcdDigoleI2C.h.

### 5.6.4.6 int const LcdDigoleI2C : :m_taille [protected]

Définition à la ligne 58 du fichier LcdDigoleI2C.h.

La documentation de cette classe a été générée à partir des fichiers suivants :

— /home/jlm-atelier/Bureau/GIT/Porte-poulailler-automatique/porte_poulailler_affichage_clavier_rtc/Lcd←-
DigoleI2C.h
— /home/jlm-atelier/Bureau/GIT/Porte-poulailler-automatique/porte_poulailler_affichage_clavier_rtc/Lcd←-
DigoleI2C.cpp

5.7 Référence de la classe LcdPCF8574 | 53

### 5.7 Référence de la classe LcdPCF8574

#include <LcdPCF8574.h>

Graphe d'héritage de LcdPCF8574 :

LcdPCF8574
# m_debug

# m_taille

# m_decalage

# m_ligne

# m_deplacement

# m_retroEclairage

+ LcdPCF8574()
+ ~LcdPCF8574()
+ init()
+ effacementAfficheur()
+ affichageUneLigne()
+ resetPos()
+ affichageDateHeure()
+ transformation()
+ affichageLumFinCourse()
+ affichageVoltage()
et 11 de plus...

LiquidCrystal_I2C

### 54 Documentation des classes

Graphe de collaboration de LcdPCF8574 :

LcdPCF8574
# m_debug

# m_taille

# m_decalage

# m_ligne

# m_deplacement

# m_retroEclairage

+ LcdPCF8574()
+ ~LcdPCF8574()
+ init()
+ effacementAfficheur()
+ affichageUneLigne()
+ resetPos()
+ affichageDateHeure()
+ transformation()
+ affichageLumFinCourse()
+ affichageVoltage()
et 11 de plus...

LiquidCrystal_I2C

Fonctions membres publiques

— LcdPCF8574 (char, const byte taille=16, const byte nbLigne=2, boolean debug=false)
— ∼LcdPCF8574 ()
— void init ()

--—initialisation for text LCD adapter--—
— void effacementAfficheur ()

--—effacement de l'afficheur-—
— void affichageUneLigne (String chaine)

-—affichage une ligne--—
— void resetPos (byte ligne)

--—reset display position and clean the line--—
— void affichageDateHeure (String jourSemaine, byte jourHeure, byte moisMinute, byte anneeSeconde)

--—affichage de la date ou de l'heure--—
— String transformation (String chaine, byte dateHeure)

--—transformation donnees date et heure--—
— void affichageLumFinCourse (unsigned int lum, byte ligne, bool siNonReglable=0)

--—affichage lumiere et fin de course--—
— void affichageVoltage (float voltage, String texte, byte ligne)

--—affichage tensions--—
— void affichageChoix (bool ouverture, bool fermeture, byte ligne)

--—affichage choix ouverture fermeture--—
— void affichageServo (int pulse, int compteRoueCodeuse, byte ligne)

5.7 Référence de la classe LcdPCF8574 | 55

--—affichage pulse et roue codeuse du servo----—
— void razLcd ()

--—remise à zero du lcd--—
— void bonjour (String chaine1, String chaine2)

--—Bonjour--—
— void cursorPosition (byte decalage, byte ligne, char ∗texte)

--—position du curseur : decalage, ligne, texte--—
— void gestionCurseur (bool curseur)

---—activation / desactivation du curseur--—
— void retroEclairage ()

--—activation / desactivation du retro eclairage---—
— void choixRetroEclairage (bool choix)

--—choix activation / desactivation du retro eclairage---—
— void cursorPositionReglages (const byte &touche, bool &relache, bool &reglage, const byte decalageSup, const byte deplacement, const byte decalageInf)

--—position du cuseur pendant les reglages--—
— byte get_m_decalage ()
— void set_m_decalage (byte decalage)

Attributs protégés

— const boolean m_debug
— int const m_taille
— byte m_decalage
— byte m_ligne
— byte m_deplacement
— bool m_retroEclairage

### 5.7.1 Description détaillée

LcdPCF8574.h (p. ??) prototype de la classe LCD circuit PCF8574 I2C afficheur lcd 2∗16 caractères avec liaison serie i2c LiquidCrystal_I2C

Définition à la ligne 13 du fichier LcdPCF8574.h.

### 5.7.2 Documentation des constructeurs et destructeur

5.7.2.1 LcdPCF8574 : :LcdPCF8574 ( char , const byte taille = 16, const byte nbLigne = 2, boolean debug = false )

Définition à la ligne 13 du fichier LcdPCF8574.cpp.

### 5.7.2.2 LcdPCF8574 : :∼LcdPCF8574 ( )

Définition à la ligne 19 du fichier LcdPCF8574.cpp.

### 56 Documentation des classes

### 5.7.3 Documentation des fonctions membres

### 5.7.3.1 void LcdPCF8574 : :affichageChoix ( bool ouverture, bool fermeture, byte ligne )

--—affichage choix ouverture fermeture--—

Définition à la ligne 156 du fichier LcdPCF8574.cpp.

Voici le graphe d'appel pour cette fonction :

LcdPCF8574::affichageChoix | LcdPCF8574::affichageUne
Ligne | LcdPCF8574::resetPos

5.7.3.2 void LcdPCF8574 : :affichageDateHeure ( String jourSemaine, byte jourHeure, byte moisMinute, byte anneeSeconde )

--—affichage de la date ou de l'heure--—

Définition à la ligne 91 du fichier LcdPCF8574.cpp.

Voici le graphe d'appel pour cette fonction :

LcdPCF8574::affichageDate
Heure

LcdPCF8574::transformation

LcdPCF8574::affichageUne
Ligne | LcdPCF8574::resetPos

5.7.3.3 void LcdPCF8574 : :affichageLumFinCourse ( unsigned int lum, byte ligne, bool siNonReglable = 0 )

--—affichage lumiere et fin de course--—

Définition à la ligne 133 du fichier LcdPCF8574.cpp.

Voici le graphe d'appel pour cette fonction :

LcdPCF8574::affichageLum
FinCourse

LcdPCF8574::affichageUne
Ligne

LcdPCF8574::cursorPosition

LcdPCF8574::resetPos

5.7 Référence de la classe LcdPCF8574 | 57

5.7.3.4 void LcdPCF8574 : :affichageServo ( int pulse, int compteRoueCodeuse, byte ligne )

--—affichage pulse et roue codeuse du servo----—

Définition à la ligne 168 du fichier LcdPCF8574.cpp.

Voici le graphe d'appel pour cette fonction :

LcdPCF8574::affichageServo

LcdPCF8574::affichageUne
Ligne

LcdPCF8574::cursorPosition

LcdPCF8574::resetPos

### 5.7.3.5 void LcdPCF8574 : :affichageUneLigne ( String chaine )

-—affichage une ligne--—

Définition à la ligne 69 du fichier LcdPCF8574.cpp.

Voici le graphe d'appel pour cette fonction :

LcdPCF8574::affichageUne
Ligne | LcdPCF8574::resetPos

### 58 Documentation des classes

Voici le graphe des appelants de cette fonction :

LcdPCF8574::affichageUne Ligne; LcdPCF8574::affichageDate Heure; LcdPCF8574::affichageLum FinCourse; LcdPCF8574::affichageVoltage; LcdPCF8574::affichageChoix; LcdPCF8574::affichageServo; LcdPCF8574::bonjour

### 5.7.3.6 void LcdPCF8574 : :affichageVoltage ( float voltage, String texte, byte ligne )

--—affichage tensions--—

Définition à la ligne 144 du fichier LcdPCF8574.cpp.

Voici le graphe d'appel pour cette fonction :

LcdPCF8574::affichageVoltage

LcdPCF8574::affichageUne
Ligne

LcdPCF8574::cursorPosition

LcdPCF8574::resetPos

### 5.7.3.7 void LcdPCF8574 : :bonjour ( String chaine1, String chaine2 )

--—Bonjour--—

Définition à la ligne 181 du fichier LcdPCF8574.cpp.

5.7 Référence de la classe LcdPCF8574 | 59

Voici le graphe d'appel pour cette fonction :

LcdPCF8574::bonjour; LcdPCF8574::gestionCurseur; LcdPCF8574::choixRetroEclairage; LcdPCF8574::effacementAfficheur; LcdPCF8574::affichageUne Ligne; LcdPCF8574::cursorPosition; LcdPCF8574::resetPos

### 5.7.3.8 void LcdPCF8574 : :choixRetroEclairage ( bool choix )

--—choix activation / desactivation du retro eclairage---—

Définition à la ligne 58 du fichier LcdPCF8574.cpp.

Voici le graphe des appelants de cette fonction :

LcdPCF8574::choixRetroEclairage | LcdPCF8574::bonjour

### 5.7.3.9 void LcdPCF8574 : :cursorPosition ( byte decalage, byte ligne, char ∗ texte )

--—position du curseur : decalage, ligne, texte--—

Définition à la ligne 204 du fichier LcdPCF8574.cpp.

### 60 Documentation des classes

Voici le graphe des appelants de cette fonction :

LcdPCF8574::cursorPosition; LcdPCF8574::affichageLum FinCourse; LcdPCF8574::affichageVoltage; LcdPCF8574::affichageServo; LcdPCF8574::bonjour

5.7.3.10 void LcdPCF8574 : :cursorPositionReglages ( const byte & touche, bool & relache, bool & reglage, const byte decalageSup, const byte deplacement, const byte decalageInf )

--—position du cuseur pendant les reglages--—

Définition à la ligne 210 du fichier LcdPCF8574.cpp.

### 5.7.3.11 void LcdPCF8574 : :effacementAfficheur ( )

--—effacement de l'afficheur-—

Définition à la ligne 35 du fichier LcdPCF8574.cpp.

Voici le graphe des appelants de cette fonction :

LcdPCF8574::effacementAfficheur | LcdPCF8574::bonjour | Généré par Doxygen

5.7 Référence de la classe LcdPCF8574 | 61

### 5.7.3.12 void LcdPCF8574 : :gestionCurseur ( bool curseur )

---—activation / desactivation du curseur--—
Définition à la ligne 199 du fichier LcdPCF8574.cpp. Voici le graphe des appelants de cette fonction :
LcdPCF8574::gestionCurseur | LcdPCF8574::bonjour

### 5.7.3.13 byte LcdPCF8574 : :get_m_decalage ( )

Définition à la ligne 225 du fichier LcdPCF8574.cpp.

### 5.7.3.14 void LcdPCF8574 : :init ( )

--—initialisation for text LCD adapter--—
Définition à la ligne 24 du fichier LcdPCF8574.cpp.

### 5.7.3.15 void LcdPCF8574 : :razLcd ( )

--—remise à zero du lcd--—
Définition à la ligne 40 du fichier LcdPCF8574.cpp.

### 5.7.3.16 void LcdPCF8574 : :resetPos ( byte ligne )

--—reset display position and clean the line--— Définition à la ligne 79 du fichier LcdPCF8574.cpp. Voici le graphe des appelants de cette fonction :

LcdPCF8574::resetPos; LcdPCF8574::affichageUne; Ligne; LcdPCF8574::affichageDate Heure; LcdPCF8574::affichageLum FinCourse; LcdPCF8574::affichageVoltage; LcdPCF8574::affichageChoix; LcdPCF8574::affichageServo; LcdPCF8574::bonjour Généré par Doxygen

### 62 Documentation des classes

### 5.7.3.17 void LcdPCF8574 : :retroEclairage ( )

--—activation / desactivation du retro eclairage---—

Définition à la ligne 47 du fichier LcdPCF8574.cpp.

### 5.7.3.18 void LcdPCF8574 : :set_m_decalage ( byte decalage )

Définition à la ligne 230 du fichier LcdPCF8574.cpp.

### 5.7.3.19 String LcdPCF8574 : :transformation ( String chaine, byte dateHeure )

--—transformation donnees date et heure--—

Définition à la ligne 114 du fichier LcdPCF8574.cpp.

Voici le graphe des appelants de cette fonction :

LcdPCF8574::transformation | LcdPCF8574::affichageDate Heure

### 5.7.4 Documentation des données membres

### 5.7.4.1 const boolean LcdPCF8574 : :m_debug [protected]

Définition à la ligne 48 du fichier LcdPCF8574.h.

### 5.7.4.2 byte LcdPCF8574 : :m_decalage [protected]

Définition à la ligne 50 du fichier LcdPCF8574.h.

### 5.7.4.3 byte LcdPCF8574 : :m_deplacement [protected]

Définition à la ligne 52 du fichier LcdPCF8574.h.

### 5.7.4.4 byte LcdPCF8574 : :m_ligne [protected]

Définition à la ligne 51 du fichier LcdPCF8574.h.

5.8 Référence de la classe Lumiere | 63

### 5.7.4.5 bool LcdPCF8574 : :m_retroEclairage [protected]

Définition à la ligne 53 du fichier LcdPCF8574.h.

### 5.7.4.6 int const LcdPCF8574 : :m_taille [protected]

Définition à la ligne 49 du fichier LcdPCF8574.h.

La documentation de cette classe a été générée à partir des fichiers suivants :
— /home/jlm-atelier/Bureau/GIT/Porte-poulailler-automatique/porte_poulailler_affichage_clavier_rtc/LcdPC←-
F8574.h
— /home/jlm-atelier/Bureau/GIT/Porte-poulailler-automatique/porte_poulailler_affichage_clavier_rtc/LcdPC←-
F8574.cpp

### 5.8 Référence de la classe Lumiere

#include <Lumiere.h>

Graphe de collaboration de Lumiere :

Lumiere
# m_lumMatin

# m_lumSoir

# m_ouverture

# m_fermeture

# m_compteurWatchdogLumiere # m_lumiereMax

# m_incrementation

# m_lumierePin

# m_rapportConvertion

# m_maxCAD

# m_heureFenetreSoir

# m_tempsLum

# m_debug

+ Lumiere()
+ ~Lumiere()
+ reglageLumiere()
+ luminositeCAD()
+ tensionLuminosite()
+ tensionLuminositeCADvers Float()
+ testLuminosite()
+ fenetreNonDeclenchement()
+ nonDeclenchementPosition Servo()
+ declenchementServoLuminosite()

et 10 de plus... Généré par Doxygen

### 64 Documentation des classes

Fonctions membres publiques
— Lumiere (const byte lumierePin, unsigned int lumMatin, unsigned int lumSoir, const byte heureFenetre←-Soir=17, const float rapportConvertion=5, const byte tempsLum=2, boolean debug=false)
— ∼Lumiere ()
— unsigned int reglageLumiere (bool matinSoir, byte touche)

--—reglage de la lumiere du matin ou du soir--—
— int luminositeCAD ()

----— lecture luminosite CAD--—
— float tensionLuminosite (int valLumiere)

----— convertion CAD vers tension luminosite --—
— float tensionLuminositeCADversFloat ()

--—lecture et convertion vers tension luminosite en float--—
— void testLuminosite ()

--—test luminosite et mise à jour du compteur watchdog lumiere--—
— void fenetreNonDeclenchement (byte horaire)

--—fenetre de non declenchement et mise à jour du compteur watchdog lumiere---—
— void nonDeclenchementPositionServo (volatile unsigned int compteRoueCodeuse, unsigned int finDe←-CourseFermeture, unsigned int finDeCourseOuverture)

--—non Declenchement Position Servo et mise à jour du compteur watchdog lumiere--—
— byte declenchementServoLuminosite ()

--—declenchement servo par la luminosite--—
— bool get_m_ouverture ()
— void set_m_ouverture (bool ouverture)
— bool get_m_fermeture ()

--—accesseur - getter--—
— void set_m_fermeture (bool fermeture)
— unsigned int get_m_lumMatin ()
— void set_m_lumMatin (unsigned int lumMatin)
— unsigned int get_m_lumSoir ()
— void set_m_lumSoir (unsigned int lumSoir)
— unsigned int get_m_compteurWatchdogLumiere ()
— void set_m_compteurWatchdogLumiere (unsigned int compteurWatchdogLumiere)

Attributs protégés
— unsigned int m_lumMatin
— unsigned int m_lumSoir

valeur de la lumière du matin
— bool m_ouverture
— bool m_fermeture
— unsigned int m_compteurWatchdogLumiere
— const unsigned int m_lumiereMax
— const byte m_incrementation
— const byte m_lumierePin
— const float m_rapportConvertion
— const int m_maxCAD
— const byte m_heureFenetreSoir
— const byte m_tempsLum
— const boolean m_debug

### 5.8.1 Description détaillée

Lumiere.h (p. ??) prototype de la classe Lumiere (p. ??) ldr

Définition à la ligne 11 du fichier Lumiere.h.

### 5.8.2 Documentation des constructeurs et destructeur

5.8.2.1 Lumiere : :Lumiere ( const byte lumierePin, unsigned int lumMatin, unsigned int lumSoir, const byte heureFenetreSoir = 17, const float rapportConvertion = 5, const byte tempsLum = 2, boolean debug = false )

Lumiere.cpp (p. ??) définitions de la classe Lumiere (p. ??) LDR

Définition à la ligne 9 du fichier Lumiere.cpp.

5.8 Référence de la classe Lumiere | 65

### 5.8.2.2 Lumiere : :∼Lumiere ( )

Définition à la ligne 17 du fichier Lumiere.cpp.

### 5.8.3 Documentation des fonctions membres

### 5.8.3.1 byte Lumiere : :declenchementServoLuminosite ( )

--—declenchement servo par la luminosite--—

Définition à la ligne 88 du fichier Lumiere.cpp.

Voici le graphe d'appel pour cette fonction :

Lumiere::declenchementServo
Luminosite | Lumiere::luminositeCAD

Voici le graphe des appelants de cette fonction :

Lumiere::declenchementServo
Luminosite | ouvFermLum | loop

### 5.8.3.2 void Lumiere : :fenetreNonDeclenchement ( byte horaire )

--—fenetre de non declenchement et mise à jour du compteur watchdog lumiere---—

Définition à la ligne 74 du fichier Lumiere.cpp.

Voici le graphe des appelants de cette fonction :

Lumiere::fenetreNonDeclenchement | ouvFermLum | loop Généré par Doxygen

### 66 Documentation des classes

### 5.8.3.3 unsigned int Lumiere : :get_m_compteurWatchdogLumiere ( )

Définition à la ligne 140 du fichier Lumiere.cpp.

Voici le graphe des appelants de cette fonction :

Lumiere::get_m_compteurWatchdog
Lumiere | routineGestionWatchdog | loop

### 5.8.3.4 bool Lumiere : :get_m_fermeture ( )

--—accesseur - getter--—

Définition à la ligne 113 du fichier Lumiere.cpp.

Voici le graphe des appelants de cette fonction :

### 5.8.3.5 unsigned int Lumiere : :get_m_lumMatin ( )

Définition à la ligne 122 du fichier Lumiere.cpp.

Voici le graphe des appelants de cette fonction :

Lumiere::get_m_lumMatin; affiLumMatin; choixLumMatin; deroulementMenu; lectureClavier; loop; temporisationAffichage; setup; Généré par Doxygen

5.8 Référence de la classe Lumiere | 67

### 5.8.3.6 unsigned int Lumiere : :get_m_lumSoir ( )

Définition à la ligne 131 du fichier Lumiere.cpp.

Voici le graphe des appelants de cette fonction :

Lumiere::get_m_lumSoir; affiLumSoir; lumiere; choixLumSoir; deroulementMenu; loop; lectureClavier; temporisationAffichage; setup; Lumiere::reglageLumiere; choixLumMatin; routineGestionWatchdog

### 5.8.3.7 bool Lumiere : :get_m_ouverture ( )

Définition à la ligne 104 du fichier Lumiere.cpp.

Voici le graphe des appelants de cette fonction :

### 5.8.3.8 int Lumiere : :luminositeCAD ( )

----— lecture luminosite CAD--—

Définition à la ligne 46 du fichier Lumiere.cpp.
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

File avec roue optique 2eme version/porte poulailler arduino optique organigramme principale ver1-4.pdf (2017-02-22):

programme principal; Initialisation; lectureClavier; Porte du poulailler arduino v1.4.1; temporisationAffichage; reglageTime; reglageDate; reglageHeureOuverture; reglageHeureFermeture; choixOuvFerm; choixLumMatin; choixLumSoir; regFinDeCourseHaut; eclairageAfficheur; regFinDeCourseBas; ouvFermLum; monteePorte; descentePorte; routineTestFermetureBoitier; routineInterrruptionAlarme2; routineInterruptionBp; routineGestionWatchdog; routineInterruptionAlarme1; routineInterruptionBoitierOuvert; accus faible; testSwitchEmissionRadio; testServo

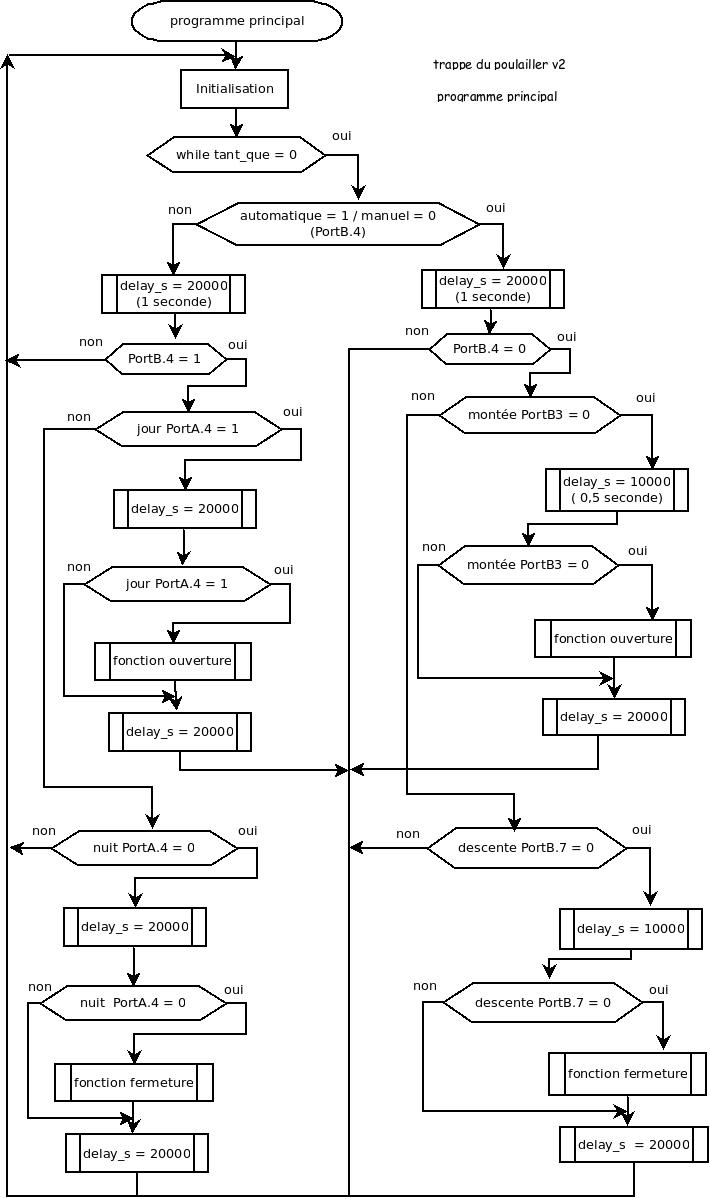
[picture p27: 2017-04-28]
avec 16c84 1ere version/ v2 organigrammes/organigramme ouverture poulailler v2 programme pincipal.jpeg

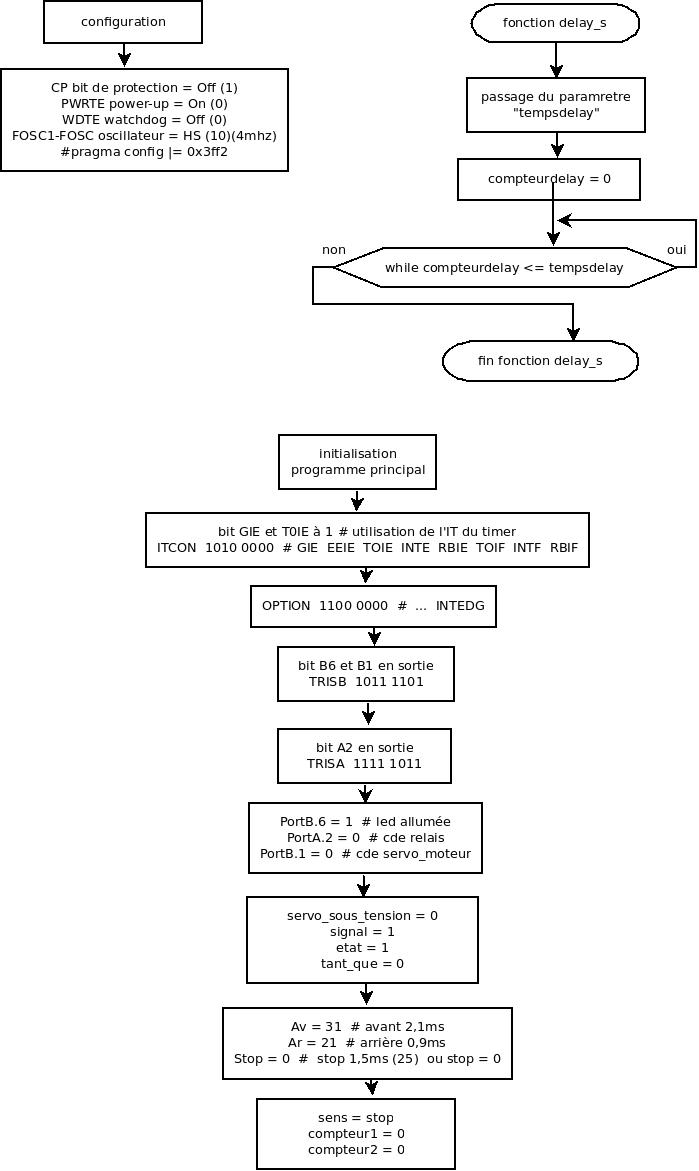
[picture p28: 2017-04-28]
avec 16c84 1ere version/ v2 organigrammes/organigramme configuration initialisation trappe poulailler v2.jpeg

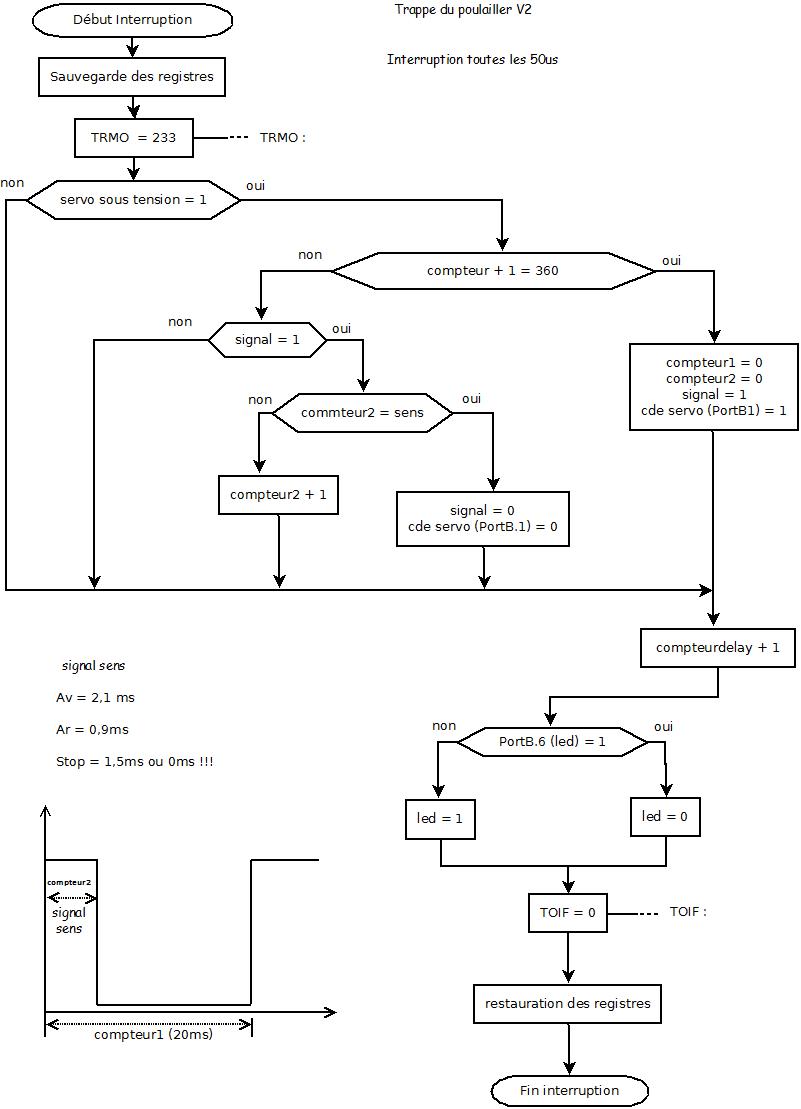
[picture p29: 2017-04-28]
avec 16c84 1ere version/ v2 organigrammes/organigramme ouverture poulailler v2 interruption.jpeg

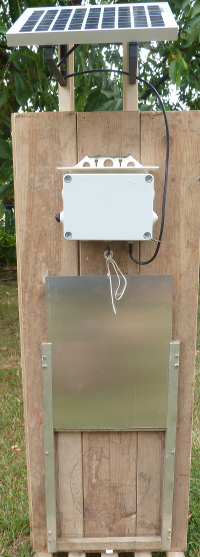
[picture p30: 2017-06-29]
avec encodeur rotatif 3eme version/Ensemble complet.png

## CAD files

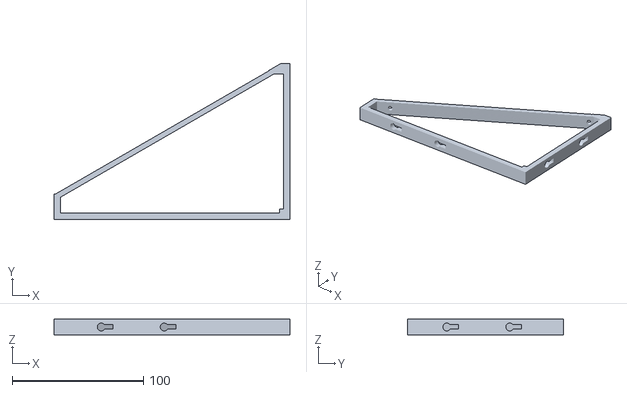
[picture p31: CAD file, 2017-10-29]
avec encodeur rotatif 3eme version/impression 3D/support_solar_pannel_fixed.stl
180.0 x 119.0 x 12.0

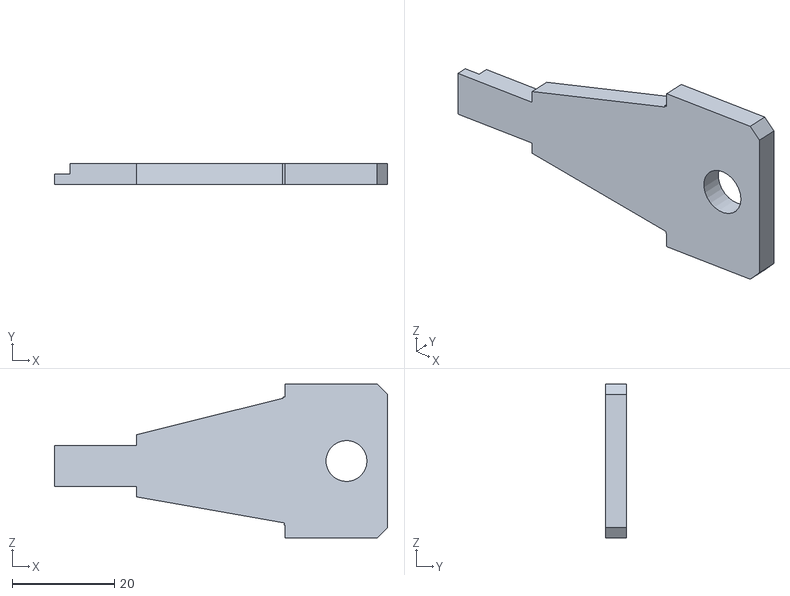
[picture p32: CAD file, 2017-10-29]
avec encodeur rotatif 3eme version/impression 3D/cle_ouverture_boitier_fixed.stl
65.0 x 4.00 x 30.0

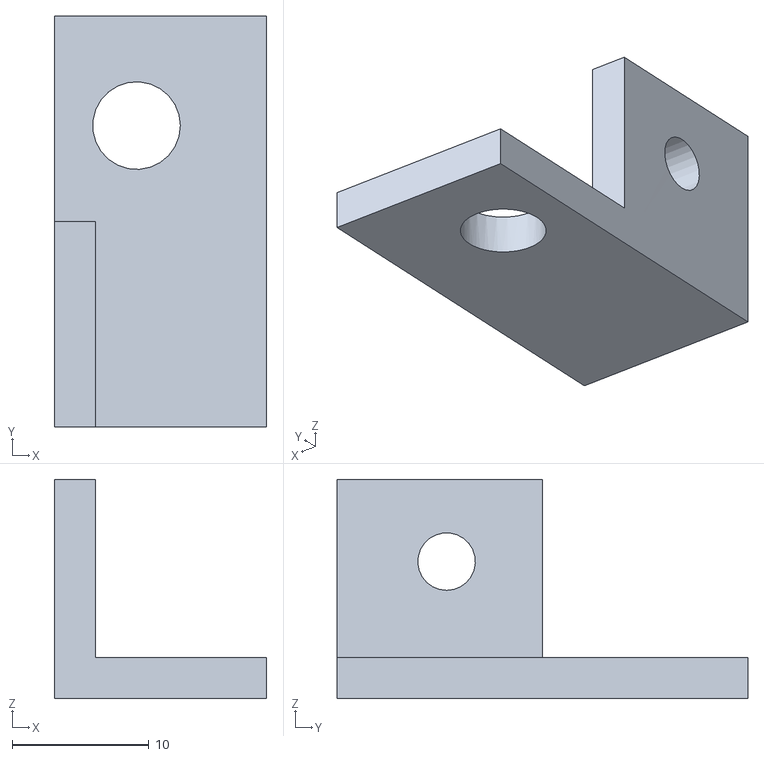
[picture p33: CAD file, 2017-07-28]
avec encodeur rotatif 3eme version/impression 3D/support_glissiere_gauche_fixed.stl
15.5 x 30.0 x 16.0

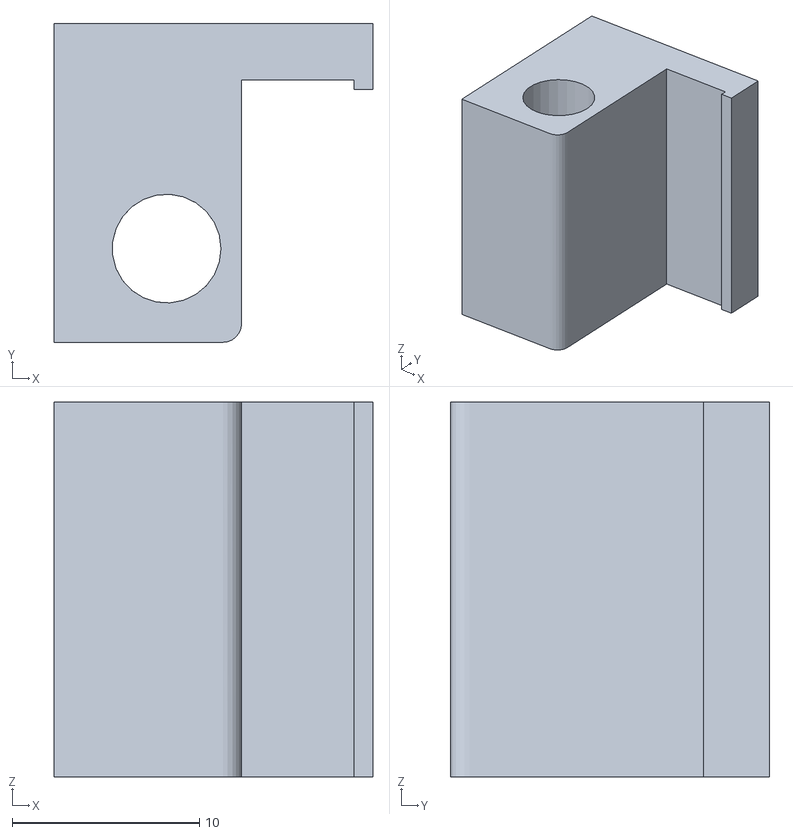
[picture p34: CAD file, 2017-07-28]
avec encodeur rotatif 3eme version/impression 3D/butoir_fixed.stl
17.0 x 17.0 x 20.0

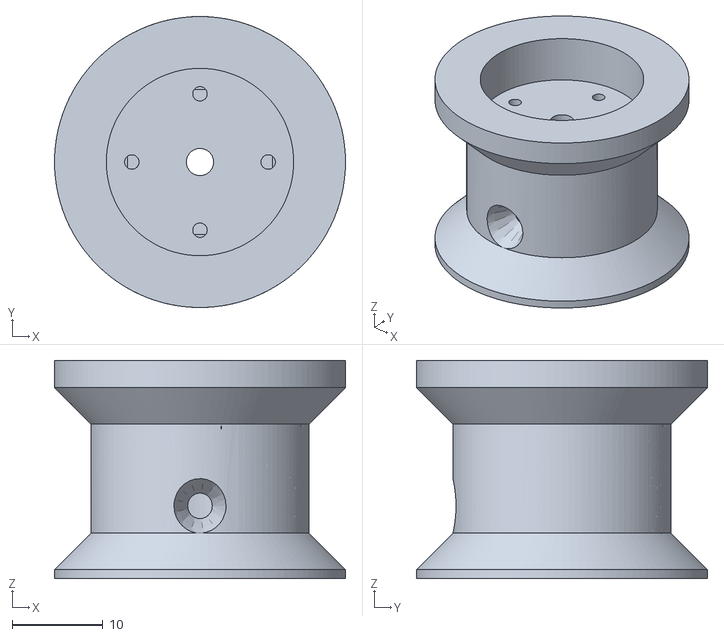
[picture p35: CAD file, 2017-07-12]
avec encodeur rotatif 3eme version/impression 3D/porte_poulailler_couronne_fixed.stl
32.0 x 32.0 x 24.0

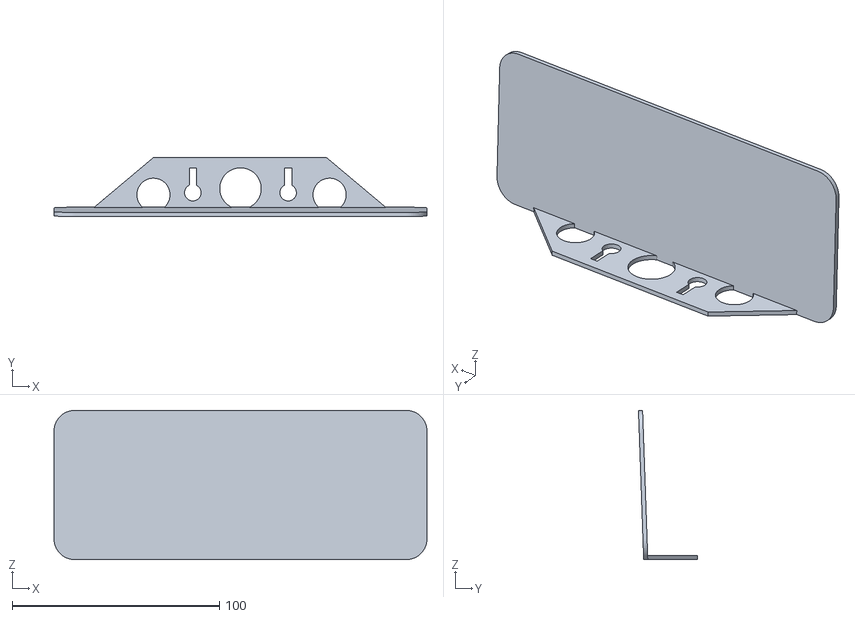
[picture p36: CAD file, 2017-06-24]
avec encodeur rotatif 3eme version/impression 3D/support_protection_pluie_fixed.stl
180.0 x 28.5 x 72.0

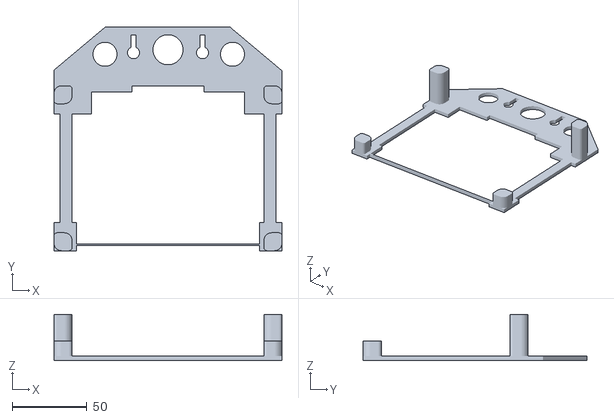
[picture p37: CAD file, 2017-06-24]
avec encodeur rotatif 3eme version/impression 3D/support_boitier_haut_fixed.stl
152.0 x 149.0 x 31.0

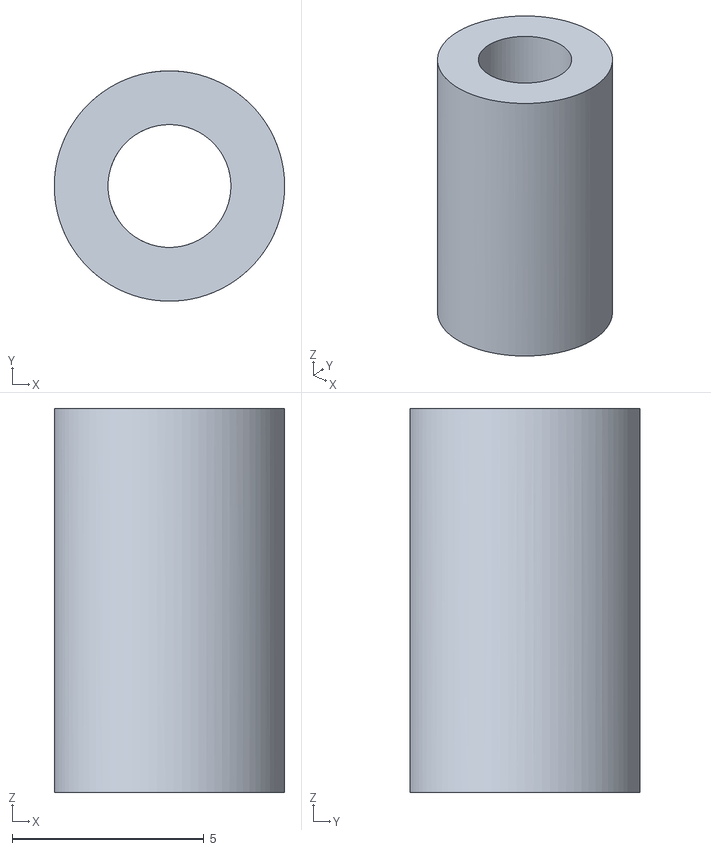
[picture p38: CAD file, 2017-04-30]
avec encodeur rotatif 3eme version/impression 3D/porte_poulailler_rondelle_fixed.stl
6.00 x 5.99 x 10.0

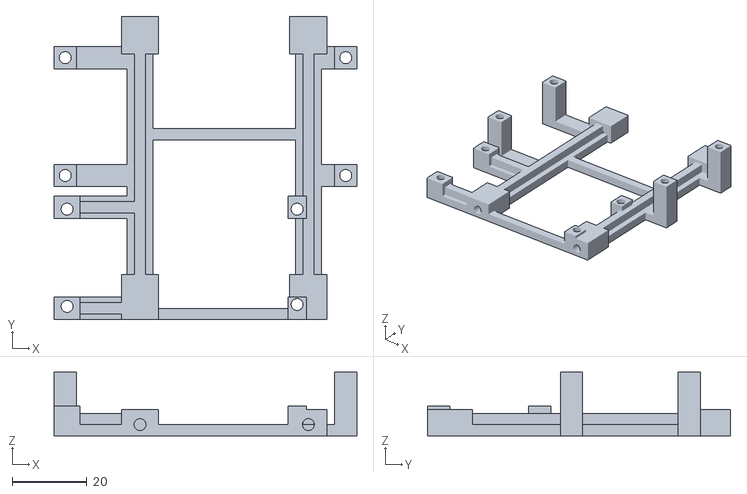
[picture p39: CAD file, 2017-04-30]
avec encodeur rotatif 3eme version/impression 3D/porte_poulailler_support_ecran_fixed.stl
81.0 x 81.0 x 17.0

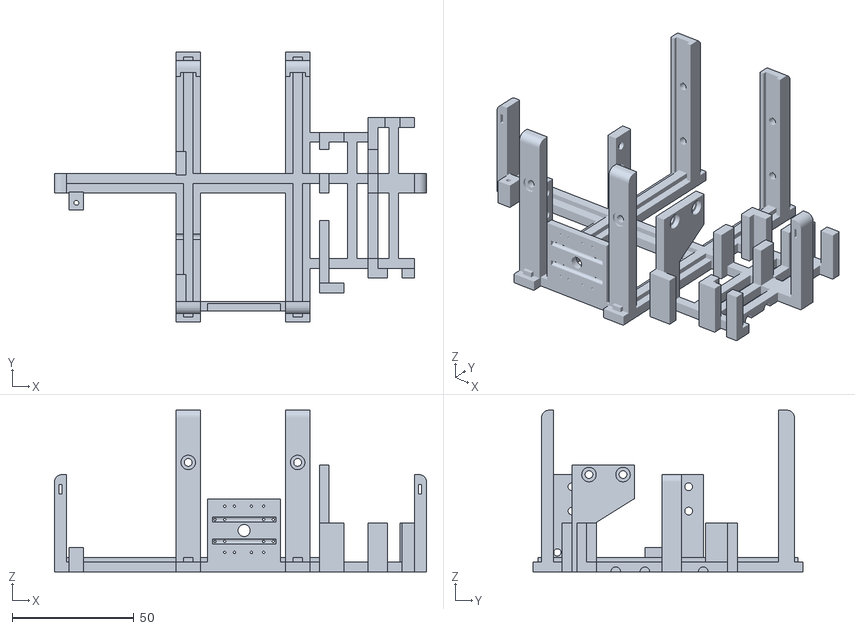
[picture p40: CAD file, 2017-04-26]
avec encodeur rotatif 3eme version/impression 3D/porte_poulailler_fixed.stl
153.0 x 111.0 x 66.5

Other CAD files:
avec encodeur rotatif 3eme version/impression 3D/support_glissiere_droite_fixed.stl

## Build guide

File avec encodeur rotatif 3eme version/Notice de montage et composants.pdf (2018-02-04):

## Montage et composants

Carte

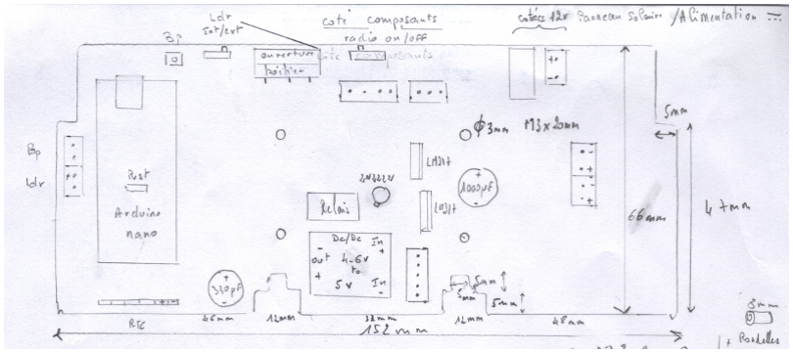
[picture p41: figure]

- Enlever toutes les leds : « power »
- nano
- lcd i2c
- rtc
- convertisseur dc-dc
Boitier
- Adaptation du support externe dans le boîtier
- perçage à 3mm du boîtier sans le support positionné. (15mm coté haut et 5mm cote bas)
- perçage à 2,35mm du support positionne dans le boîtier.
- 4x vis de 8xM3

Composants

- Boîtier 3012-S
- 2x crochets 30x10x3mm
- Arduino nano avec ses connecteurs
- RTC DS3231 avec son connecteur – module ZS-042
- CR2032 ou LIR2032 (voir fin du document)
- Emetteur radio 433Mhz
- LCD 2x16 caractères et sa carte I2C (voir fin du document pour l’adresse du module I2C). Pas de bleu
- Clavier 5 touches
- Régulateur DC DC (2,5v/6v to 4v/12v 1A)
- 2x batteries NIMH 2500mAh 4,8v
- encodeur rotatif. Peut être inversé...variable m_compteurRoueCodeuse (++ et – à inverser)
- servo moteur MG995 avec son adaptateur 3D
- 2x 2,7k pour la modification du servo moteur (rotation 360°]
- relais 5v G5V-01
- 2N2222A
- 2x LM317T
- 3x 1N4007
- 6x 1N4148 + 1 pour Buzzer (à souder entre D7 et +5v R14)
- 2x diodes Schottky 1N5819
- 1000uf – 330uf – 6x 100nf - 5x 1uf - 3x10uf - 6x1nf - 0,047uf
- 2x27 - 1k - 8x 10k - 2x 4,7k - 2x 15k/16k
- 2x ldr
- 2x zener 5,6v
- 2x led verte
- 3x commutateurs
- switch à lamelle
- bouton poussoir interne
- bouton poussoir étanche externe

- prise interne jack mâle 2,1x5,5mm pour panneau ou alimentation par bloc secteur de 12v
- prise externe pour panneau solaire
- aimant percé 19x4mm.
- 4x contacts sous verre (reed)
- connecteurs et câbles : 5, 3, 4 et 6x 2
- barrettes connecteurs femelles/mâles
- panneau solaire et son câble (80cm) avec prise, ainsi que son support
- 4 vis 10xM3 à 8xm3 , clé 7x32
- câble 2 fils 80cm
- diode anti-retour 1N5819
- prise alimentation jack femelle 2,1x5,5mm
- 4 vis 3,5x20mm te fraisée + chevilles
- écartement de 48mm des fixations de chaque support
- 3D :
- support principale
- bobine
- cordelette 2mm x 65cm
- adaptateur entre la bobine et le servo (plastique ou métallique, diamètres différents)
- 4 petites vis bois 8x1,5mm pour la liaison entre l’adaptateur et la bobine
- vis 8x2mm pour fixer l’ensemble bobine sur le servo
- support clavier / lcd
- 4 rondelles
- support boitier
- protège pluie
- 2 supports panneau solaire
- 4 supports de glissière (2 droits et 2 gauches)
- vis et écrous
- 4 20xM3 ,2 écrous et 4 rondelles pour la carte
- 4 10xM3 à 15xM3 et quatre écrous pour le servo
- 2 8xM3 à 10xM3 pour l’encodeur
- 4 6xM3 à 15xM3 pour l’afficheur
- 4 6xM3 à 10xM3 pour le clavier
- 2 10xM3 pour le support clavier / afficheur coté bobine
- 1 10xM3 pour le rtc
- 2 15xM… et deux écrous pour le contact d’ouverture du boitier
- 2 10xM2 , 2 écrous M2 pour le microswitch TIAITHUA GO10985
Glissières en aluminium ou bois, Porte en aluminium.
- 4x baguettes aluminium 19,5mm x 2mm x 500mm
- 2x baguettes aluminium 11,5mm x 2mm x 500mm
- 6x vis bois 3,5x20mm
- 4x vis bois 4,5x40mm
- baguette bois 21x15x1500mm
- butée
- 4x vis bois 4x40mm

- vis bois 3x20mm
- 1x plaque aluminium 250mm x 0,8mm x 500mm
- cordelette de 30cm environ.
- Découper la plaque aux dimensions suivantes : 25 x 33cm
- Percer la plaque diamètre 3mm au centre à 0,5cm du haut, pour la cordelette.
- Positionner les baguettes pour former deux glissières. Les coller pour le travaille de perçage.
- Percer les baguettes à 3cm, 14cm de chaque coté et au centre (25cm) : diamètre 3mm.
- 6x Vis bois de 3,5 x 20mm.
- Faire deux trous à 7cm de chaque coté , diamètre 5mm, pour la fixation sur le support.
- 4 vis bois 4,5x40mm
- Construire le cadre support des glissières avec des baguettes de bois imputrescible (21 x15 mm) .
- 2 baguettes de 50cm
- 2 baguettes de 24cm espacées de 30cm (ouverture de la porte).
- 4 vis 4x40mm
- butée avec vis 3x20mm
- Mettre la plaque dans les glissière
- Poser les glissière avec un peu de jeu
- Fixer le butoir
- vis bois de 3x20mm

Glissières en aluminium, Porte en plexiglas de 5mm.
- 2x baguettes tubes carrés aluminium 11,5mm x M8 x 500mm
- 2x cornières aluminium 11,5mm x 19,5mm x 500mm
- 1x tube rond aluminium 7,5mm x M5 x 230mm taraude M6 de chaque coté
- 1x tige filetée 7mm x 280mm
- 6x écrous 6x10mm
- 2x rondelles 46x14mm
- 2x vis métaux 6x30mm
- 2 supports de glissière gauche en 3D
- 2 supports de glissière droit en 3D
- butée
- 1x plaque plexiglas 250mm x 5mm x 332mm
- cordelette de 30cm environ.
- Percer 2 trous centrés de 6mm à 10mm et 19mm en partant de chaque coté du tube.
- Positionner le plus grand coté de la cornière sur le tube carré.
- Percer la cornière.
- Mettre la butée avec deux écrous au milieu de la tige filetée.
- Positionner la tige filetée en bas et le tube taraudé en haut.
- Mettre les supports de glissière puis les vis et écrous (avec rondelle sur l’extérieur).
- Régler l’écartement à 230mm puis serrer.
- Percer la plaque au centre à 10mm du bord haut avec un trou entre 4 et 5mm.
- Mettre la cordelette.

LCD_I2C

Le module Backpack I2C peut être livré soit avec un PCF857AT, soit un PCF8574T (lisible sur le composant).

L'adresse du module sur le bus I2C dépend:
1. Du circuit utilisé
2. Et des pontages d'adresse A0, A1, A2

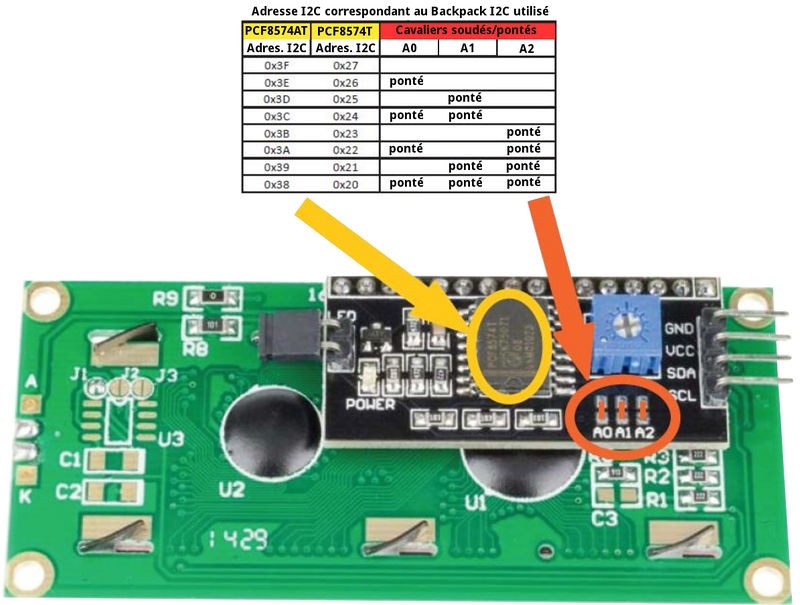
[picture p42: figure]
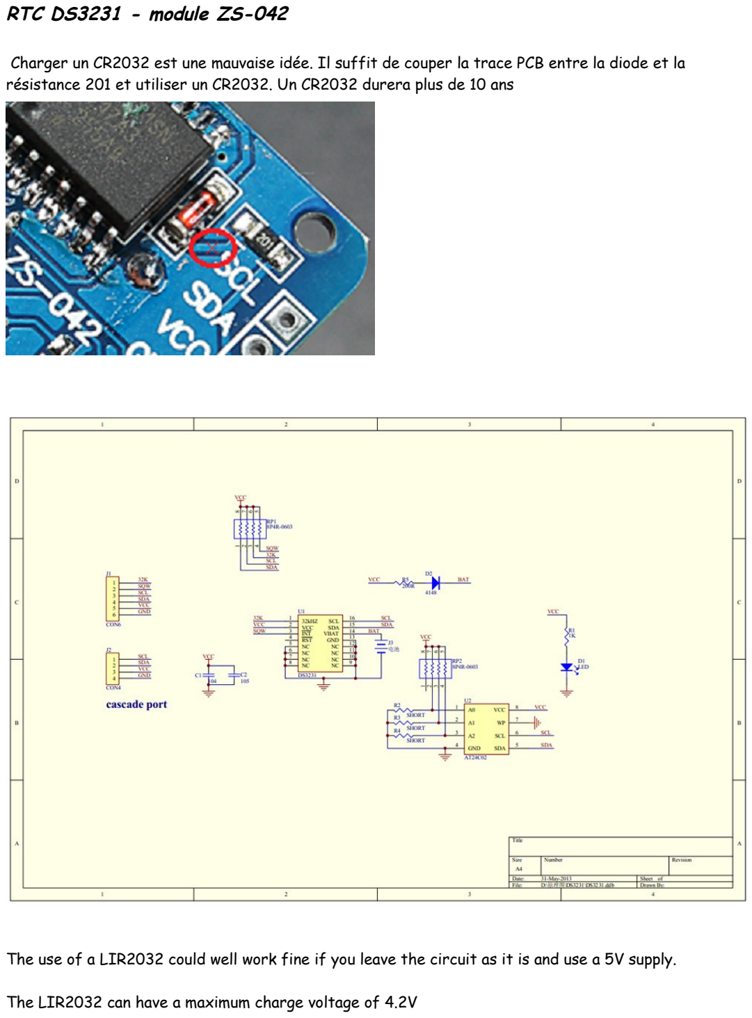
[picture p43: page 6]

RTC DS3231 - module ZS-042

Charger un CR2032 est une mauvaise idée. Il suffit de couper la trace PCB entre la diode et la résistance 201 et utiliser un CR2032. Un CR2032 durera plus de 10 ans

The use of a LIR2032 could well work fine if you leave the circuit as it is and use a 5V supply.

The LIR2032 can have a maximum charge voltage of 4.2V

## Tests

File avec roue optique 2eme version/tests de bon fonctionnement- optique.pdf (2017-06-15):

# Test matériel et logiciel du boîtier - porte de poulailler automatique

### Fonctionnement global : ok – ajout d’un support externe au boitier

Affichage : pour un même LCD : deux types de liaisons possibles en I2C : PIC et PCF8574

Clavier : pb touche 4 difficile – résolu par la modification du délais de 100 à 50ms

Bouton poussoir : le bouton a beaucoup de rebonds ; modification du debounce à 150ms et délais de 50ms pour le relâche du bouton

Servo moteur : modifie pour un fonctionnement sur 360°

### Contacts fin de course : ok avec les ressorts

Horloge : stable et test au démarrage de la présence de la carte

Température : précision de 0,25°C

Capteur de lumière : faux contact sur capteur de lumière. résolu

Batteries : deux batteries 4,8v nimh – supporte les températures hautes et basses

Charge batteries : tension batterie chargée < à 5,7v. Charge lente en courant uniquement

Emetteur radio : ok - ajout d’un commutateur on/off émission radio en broche A2

### Alimentation 5v : stable à 5,12v

### Roue codeuse : stable

Arduino nano : mémoire restante de 1030octets sur 2048

### Réglages : date : ok heure : ok heure ouverture : ok heure fermeture : ok lumière matin : ok lumière soir : ok choix ouverture : ok fin de course fermeture : ok fin de course ouverture : ok

### Sécurité : par contact fin de course et logiciel

### Ouverture / fermeture boîtier : ok

Message radio : ajout du message de la sram restante pour les tests de durée

### Tests de bon fonctionnement : RAS

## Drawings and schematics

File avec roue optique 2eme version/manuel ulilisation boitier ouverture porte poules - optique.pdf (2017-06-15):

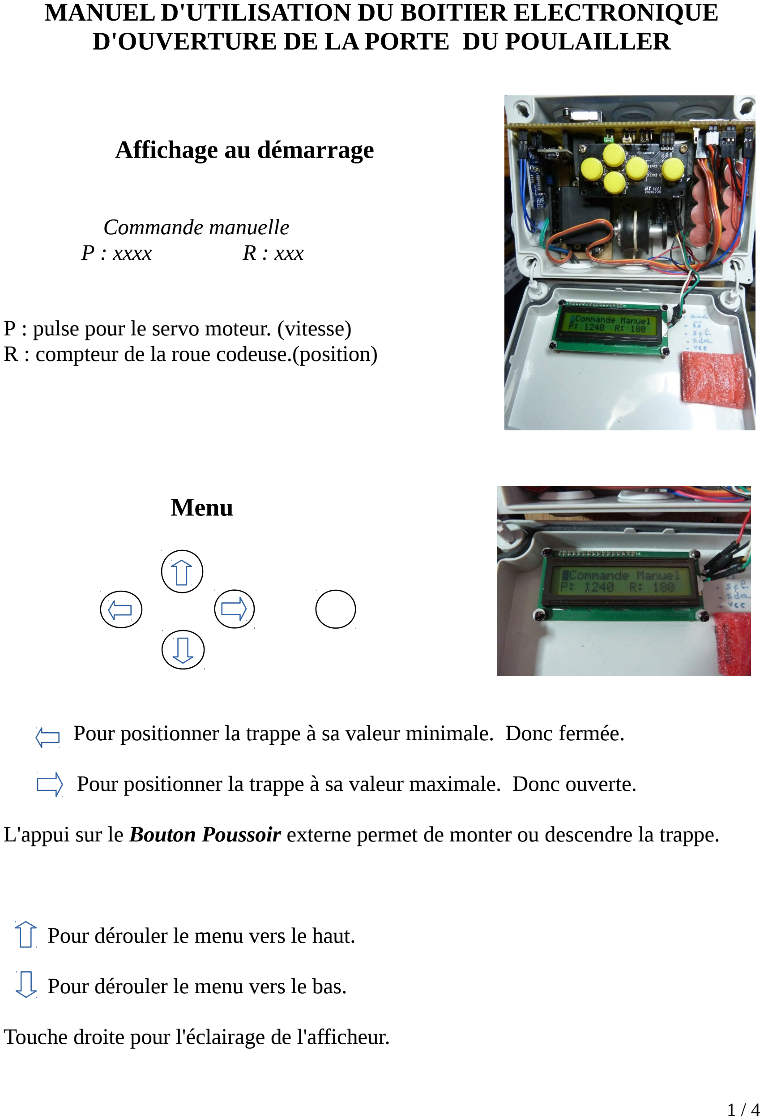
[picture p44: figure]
MANUEL D'UTILISATION DU BOITIER ELECTRONIQUE D'OUVERTURE DE LA PORTE DU POULAILLER; Affichage au démarrage; Commande manuelle; P : xxxx; R : xxx; Menu; Pour dérouler le menu vers le haut.; Pour dérouler le menu vers le bas.

P : pulse pour le servo moteur. (vitesse)
R : compteur de la roue codeuse.(position)

Pour positionner la trappe à sa valeur minimale. Donc fermée.

Pour positionner la trappe à sa valeur maximale. Donc ouverte.

L'appui sur le Bouton Poussoir externe permet de monter ou descendre la trappe.

Touche droite pour l'éclairage de l'afficheur.

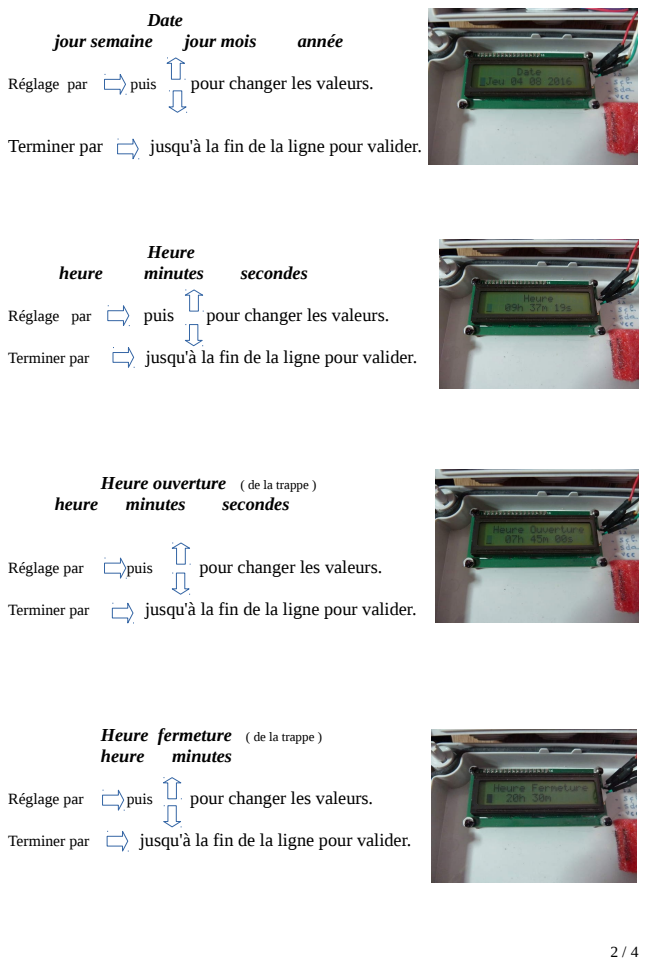
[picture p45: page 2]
Date; jour semaine; jour mois; année; Réglage par; puis; pour changer les valeurs.; Terminer par; jusqu'à la fin de la ligne pour valider.; Heure; heure; minutes; secondes

Heure ouverture ( de la trappe )

Heure fermeture ( de la trappe )

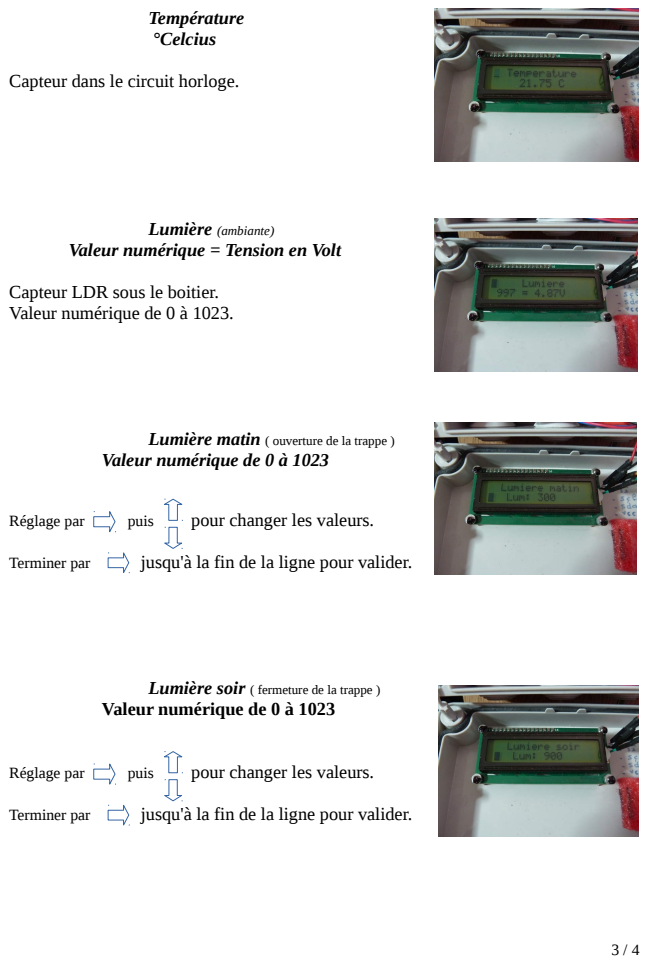
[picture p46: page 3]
Température °Celcius; Lumière (ambiante); Réglage par; puis; pour changer les valeurs.; Terminer par; jusqu'à la fin de la ligne pour valider.

Capteur dans le circuit horloge.

Valeur numérique = Tension en Volt

Capteur LDR sous le boitier.
Valeur numérique de 0 à 1023.

Lumière matin ( ouverture de la trappe )
Valeur numérique de 0 à 1023

Lumière soir ( fermeture de la trappe )

Choix d'ouverture et de fermeture

ouverture : heure / lumière

fermeture : heure / lumière

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

Fin de course haut
Valeur numérique de 0 à 1023 ( correspond à la position )

haute de la trappe par défaut = 250

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

Fin de course bas
Valeur numérique de 0 à 1023 ( correspond à la position )

haute de la trappe par défaut = 150

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

Tension de la batterie commande en Volt
et valeur numérique 0 à 1023
et
Tension de la batterie servo-moteur en Volt
et valeur numérique 0 à 1023

batteries de 4,8v / 2500 mAh chargée : 5,6v / déchargée : 4,4v

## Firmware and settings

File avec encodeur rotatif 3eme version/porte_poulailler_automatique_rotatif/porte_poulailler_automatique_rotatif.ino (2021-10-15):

/**@file*/
/**
    \porte du poulailler avec encodeur rotatif v2.0.4
    \file porte_poulailler_affichage_clavier_rtc
    \brief Automatisation de la porte du poulailler en utilisant l'heure ou la lumière.
    \details Simplification d'utilisation. Electronique avec microcontroleur, alimentée par batterie, couplée à un capteur solaire.
    \author Zephyr5028
    \juin 2017
*/
/**
    porte-poulailler : affichage + clavier + rtc
*/

/**
  31 01 2020 : modification du choix ouverture fermeture avec l'ajout de manuel (heure,lumiere,manuel)
  12 01 2020 : branche choix ouverture fermeture en cours
    
  12 01 2020 : passage version v2.0.4, pour petites modifications : 
                    - affichage n serie du boitier au demarrage,
                    - type manuel pour l'ouverture du boitier
                    - servo reglé par un potentiometre interne 10k
                    - ldr etanche
                    - bouton etanche
                    - parametre demarrage ouverture 40
  17 12 2017 : parametres des boitiers dans le programme
  15 12 2017 : passage à la version v2.0.3
  10 12 2017 : amélioration de la lecture de la tension des batteries avec l'utilisation de AREF interne (1.1v)
  28 07 2017 : prise en compte du buzzer. Signal avant la fermeture de la porte
  13 07 2017 : securité à la fermeture en cas de rembobinage inverse de la cordelette
  12 07 2017 : intégration du numéro du boitier dans le message radio
     06 2017 : texte envoyé par radio, convertir la lumière en lux, convertir la course de la porte en cm, menu affichage fin de course ouverture
     03 2017 : encodeur rotatif.
     01 2017 : classes radio, lcd (digole et liquidcrystal), horloge, bouton.
  29 12 2016 : classe Codeur (optique).
  28 12 2016 : classe Lumiere.
  26 12 2016 : classe Accus.
  21 12 2016 : ajout de la classe servo.
  01 12 2016 : first commit sur gihub.
  20 09 2016 : classe clavier.
  19 09 2016 : suppression du blocage au demarrage (si = 200).
  18 09 2016 : en cas de probleme avec le sens de rotation du servo :
                  - variable globale : sens.
                  - arret fin de course ( contact) quelque soit le sens.
                  - diminution de la vitesse reduite dans la descente de la trappe (inertie).
  17 09 2016 : problème avec servotimer2  :
                  - Le pulse en ms ne fonctionne pas donc le servo est tjs dans le même sens (hs).
                  - Les valeurs du pulse étaient mauvaise.
                  - Il faut :
                        90° : 1500ms.
                         0° : 1000ms.
                       180° : 2000ms.
  10 09 2016 :
                 - affichage compteur roue codeuse envoi radio.
                 - delay d'attente de la remontée du servo augmentée : 300.
  Important :
    -with ServoTimer2 et VirtualWire.
    -il faut commenter typedef dans la bibliothèque servotimer2.
*/
/*
           nom macro  valeur de la macro                                forme syntaxique
           __LINE__  numéro de la ligne courante du programme source   entier
           __FILE__  nom du fichier source en cours de compilation     chaîne
           __DATE__  la date de la compilation                         chaîne
           __TIME__  l'heure de la compilation                         chaîne
           __STDC__  1 si le compilateur est ISO, 0 sinon              entier
*/

#define SERVO_TEST false// pour utiliser (true) ou non (false) le test du servomoteur

/**-------boitiers......*/
//#define BOITIER_N001  // boitier n1
//#define BOITIER_N002  // boitier n2
//#define BOITIER_N003  // boitier n3
//#define BOITIER_N004  // boitier n4
//#define BOITIER_N005  // boitier n5
#define BOITIER_N006  // boitier n6

/*--------------------------------------------------------------------------------*/
#if defined(BOITIER_N001)
const char affichageBonjour[] PROGMEM = "   Porte N001   . Version 2.0.4  .Porte Poulailler.Manque carte RTC";
const char numeroSerieBoitier[] = "N001;\0"; // numero de serie du boitier
#define SERVO_PULSE_STOP 1450 // value should usually be 750 to 2200 (1500 = stop)
#define SERVO_PULSE_OUVERTURE_FERMETURE  220  // vitesse d'ouverture ou fermeture ( 1500 +/- 140)
#define SERVO_PULSE_OUVERTURE_FERMETURE_REDUIT  160  // vitesse réduite d'ouverture ou fermeture ( 1500 +/- 100)
#define TEMPO_ENCODEUR  5  // tempo pour éviter les rebonds de l'encodeur ms
#define FOURCHETTE_FERMETURE  10 // - pas de l'encodeur rotatif
#define FOURCHETTE_OUVERTURE  5 // + pas de l'encodeur rotatif
#define LUMIERE_BOUCLES  4  //  boucles pour valider l'ouverture / fermeture avec la lumière (compteur watchdog)
#define OFFSET_AREF -0.00 // offset de la tension de reference aref (1.1v), = +/-0.08v theorique
#define SENS 1 // sens pour le compteur m_compteRoueCodeuse++; et m_compteRoueCodeuse--; de la classe JlmRotaryEncoder
/// choisir entre un afficheur lcd I2C de type Digole (PICF182) ou de type LiquidCrystal (PCF8574)
#define LCD_LIQIDCRYSTAL  // utilisation de lcd liquid crystal I2C - PCF8574
/// Set the LCD address to 0x27 for a 16 chars and 2 line display pour pcf8574t / si pcf8574at alors l'adresse est 0x3f
//#define PCF8574AT // liquid crystal i2c avec pcf8574at @03f
#define PCF8574T // liquid crystal i2c avec pcf8574t @027
#define ROUE_CODEUSE_POSITION_DEFAUT_FIN_DE_COURSE_FERMETURE  30// initialisation par defaut au demarrage de la valeur de fin de course fermeture
/*--------------------------------------------------------------------------------*/
#elif defined(BOITIER_N002)
const char affichageBonjour[] PROGMEM = "   Porte N002   . Version 2.0.4  .Porte Poulailler.Manque carte RTC";
const char numeroSerieBoitier[] = "N002;\0"; // numero de serie du boitier
#define SERVO_PULSE_STOP 1450 // value should usually be 750 to 2200 (1500 = stop), a tester pour chaque servo
#define SERVO_PULSE_OUVERTURE_FERMETURE  220  // vitesse d'ouverture ou fermeture ( 1500 +/- 140)
#define SERVO_PULSE_OUVERTURE_FERMETURE_REDUIT  160  // vitesse réduite d'ouverture ou fermeture ( 1500 +/- 100)
#define TEMPO_ENCODEUR  15  // tempo pour éviter les rebonds de l'encodeur ms
#define FOURCHETTE_FERMETURE  10 // - pas de l'encodeur rotatif
#define FOURCHETTE_OUVERTURE  5 // + pas de l'encodeur rotatif
#define LUMIERE_BOUCLES  4  //  boucles pour valider l'ouverture / fermeture avec la lumière (compteur watchdog)
#define OFFSET_AREF -0.07 // offset de la tension de reference aref (1.1v), = +/-0.08v theorique
#define SENS 1 // sens pour le compteur m_compteRoueCodeuse++; et m_compteRoueCodeuse--; de la classe JlmRotaryEncoder
/// choisir entre un afficheur lcd I2C de type Digole (PICF182) ou de type LiquidCrystal (PCF8574)
//#define LCD_DIGOLE  // utilisation de lcd avec circuit I2C Digole - PIC16F182
#define LCD_LIQIDCRYSTAL  // utilisation de lcd liquid crystal I2C - PCF8574
/// Set the LCD address to 0x27 for a 16 chars and 2 line display pour pcf8574t / si pcf8574at alors l'adresse est 0x3f
//#define PCF8574AT // liquid crystal i2c avec pcf8574at @03f
#define PCF8574T // liquid crystal i2c avec pcf8574t @027
#define ROUE_CODEUSE_POSITION_DEFAUT_FIN_DE_COURSE_FERMETURE  30// initialisation par defaut au demarrage de la valeur de fin de course fermeture
/*--------------------------------------------------------------------------------*/
#elif defined(BOITIER_N003)
const char numeroSerieBoitier[] = "N003;\0"; // numero de serie du boitier
const char affichageBonjour[] PROGMEM = "Porte Poulailler. Version 2.0.3  .Porte Poulailler.Manque carte RTC";
#define SERVO_PULSE_STOP 1388 // value should usually be 750 to 2200 (1500 = stop), a tester pour chaque servo
#define SERVO_PULSE_OUVERTURE_FERMETURE  220  // vitesse d'ouverture ou fermeture ( 1500 +/- 140)
#define SERVO_PULSE_OUVERTURE_FERMETURE_REDUIT  150  // vitesse réduite d'ouverture ou fermeture ( 1500 +/- 100)
#define TEMPO_ENCODEUR  5  // tempo pour éviter les rebonds de l'encodeur ms
#define FOURCHETTE_FERMETURE  16 // - pas de l'encodeur rotatif
#define FOURCHETTE_OUVERTURE  12 // + pas de l'encodeur rotatif
#define LUMIERE_BOUCLES  4  //  boucles pour valider l'ouverture / fermeture avec la lumière (compteur watchdog)
#define OFFSET_AREF -0.08 // offset de la tension de reference aref (1.1v), = +/-0.08v theorique
#define SENS 1 // sens pour le compteur m_compteRoueCodeuse++; et m_compteRoueCodeuse--; de la classe JlmRotaryEncoder
/// choisir entre un afficheur lcd I2C de type Digole (PICF182) ou de type LiquidCrystal (PCF8574)
//#define LCD_DIGOLE  // utilisation de lcd avec circuit I2C Digole - PIC16F182
#define LCD_LIQIDCRYSTAL  // utilisation de lcd liquid crystal I2C - PCF8574
/// Set the LCD address to 0x27 for a 16 chars and 2 line display pour pcf8574t / si pcf8574at alors l'adresse est 0x3f
//#define PCF8574AT // liquid crystal i2c avec pcf8574at @03f
#define PCF8574T // liquid crystal i2c avec pcf8574t @027
#define ROUE_CODEUSE_POSITION_DEFAUT_FIN_DE_COURSE_FERMETURE  30// initialisation par defaut au demarrage de la valeur de fin de course fermeture
/*--------------------------------------------------------------------------------*/
#elif defined(BOITIER_N004)
const char numeroSerieBoitier[] = "N004;\0"; // numero de serie du boitier
const char affichageBonjour[] PROGMEM = "Porte Poulailler. Version 2.0.2  .Porte Poulailler.Manque carte RTC";
#define SERVO_PULSE_STOP 1474 // value should usually be 750 to 2200 (1500 = stop), a tester pour chaque servo
#define SERVO_PULSE_OUVERTURE_FERMETURE  220  // vitesse d'ouverture ou fermeture ( 1500 +/- 140)
#define SERVO_PULSE_OUVERTURE_FERMETURE_REDUIT  160  // vitesse réduite d'ouverture ou fermeture ( 1500 +/- 100)
#define TEMPO_ENCODEUR  5  // tempo pour éviter les rebonds de l'encodeur ms
#define FOURCHETTE_FERMETURE  10 // - pas de l'encodeur rotatif
#define FOURCHETTE_OUVERTURE  5 // + pas de l'encodeur rotatif
#define LUMIERE_BOUCLES  4  //  boucles pour valider l'ouverture / fermeture avec la lumière (compteur watchdog)
#define OFFSET_AREF -0.08 // offset de la tension de reference aref (1.1v), = +/-0.08v theorique
#define SENS 1 // sens pour le compteur m_compteRoueCodeuse++; et m_compteRoueCodeuse--; de la classe JlmRotaryEncoder
/// choisir entre un afficheur lcd I2C de type Digole (PICF182) ou de type LiquidCrystal (PCF8574)
//#define LCD_DIGOLE  // utilisation de lcd avec circuit I2C Digole - PIC16F182
#define LCD_LIQIDCRYSTAL  // utilisation de lcd liquid crystal I2C - PCF8574
/// Set the LCD address to 0x27 for a 16 chars and 2 line display pour pcf8574t / si pcf8574at alors l'adresse est 0x3f
#define PCF8574AT // liquid crystal i2c avec pcf8574at @03f
//#define PCF8574T // liquid crystal i2c avec pcf8574t @027
#define ROUE_CODEUSE_POSITION_DEFAUT_FIN_DE_COURSE_FERMETURE  30// initialisation par defaut au demarrage de la valeur de fin de course fermeture
/*--------------------------------------------------------------------------------*/
// BOITIER_N005 : le boitier n005 est un recepteur avec un montage electronique different.
/*--------------------------------------------------------------------------------*/
#elif defined(BOITIER_N006)
const char affichageBonjour[] PROGMEM = "   Porte N006   . Version 2.0.4  .Porte Poulailler.Manque carte RTC";
const char numeroSerieBoitier[] = "N006;\0"; // numero de serie du boitier
#define SERVO_PULSE_STOP 1474 // value should usually be 750 to 2200 (1500 = stop), a tester pour chaque servo
#define SERVO_PULSE_OUVERTURE_FERMETURE  220  // vitesse d'ouverture ou fermeture ( 1500 +/- 140)
#define SERVO_PULSE_OUVERTURE_FERMETURE_REDUIT  100  // vitesse réduite d'ouverture ou fermeture ( 1500 +/- 100)
#define TEMPO_ENCODEUR  5  // tempo pour éviter les rebonds de l'encodeur ms
#define FOURCHETTE_FERMETURE  16 // - pas de l'encodeur rotatif
#define FOURCHETTE_OUVERTURE  12 // + pas de l'encodeur rotatif
#define LUMIERE_BOUCLES  4  //  boucles pour valider l'ouverture / fermeture avec la lumière (compteur watchdog)
#define OFFSET_AREF -0.07 // offset de la tension de reference aref (1.1v), = +/-0.08v theorique
#define SENS 0 // sens pour le compteur m_compteRoueCodeuse++; et m_compteRoueCodeuse--; de la classe JlmRotaryEncoder
/// choisir entre un afficheur lcd I2C de type Digole (PICF182) ou de type LiquidCrystal (PCF8574)
//#define LCD_DIGOLE  // utilisation de lcd avec circuit I2C Digole - PIC16F182
#define LCD_LIQIDCRYSTAL  // utilisation de lcd liquid crystal I2C - PCF8574
/// Set the LCD address to 0x27 for a 16 chars and 2 line display pour pcf8574t / si pcf8574at alors l'adresse est 0x3f
/// pcb lcm1602 with pcf8574t
//#define PCF8574AT // liquid crystal i2c avec pcf8574at @03f
#define PCF8574T // liquid crystal i2c avec pcf8574t @027
#define ROUE_CODEUSE_POSITION_DEFAUT_FIN_DE_COURSE_FERMETURE  30// initialisation par defaut au demarrage de la valeur de fin de course fermeture
/*--------------------------------------------------------------------------------*/
#else
// parametres par defaut
const char numeroSerieBoitier[] = "N00x;\0"; // numero de serie du boitier
const char affichageBonjour[] PROGMEM = "Porte Poulailler. Version 2.0.x  .Porte Poulailler.Manque carte RTC";
#define SERVO_PULSE_STOP 1500 // value should usually be 750 to 2200 (1500 = stop), a tester pour chaque servo
#define SERVO_PULSE_OUVERTURE_FERMETURE  140  // vitesse d'ouverture ou fermeture ( 1500 +/- 140)
#define SERVO_PULSE_OUVERTURE_FERMETURE_REDUIT  100  // vitesse réduite d'ouverture ou fermeture ( 1500 +/- 100)
#define TEMPO_ENCODEUR  5  // tempo pour éviter les rebonds de l'encodeur ms
#define FOURCHETTE_FERMETURE  10 // - pas de l'encodeur rotatif
#define FOURCHETTE_OUVERTURE  5 // + pas de l'encodeur rotatif
#define LUMIERE_BOUCLES  4  //  boucles pour valider l'ouverture / fermeture avec la lumière (compteur watchdog)
#define OFFSET_AREF -0.00 // offset de la tension de reference aref (1.1v), = +/-0.08v theorique
#define SENS 1 // sens pour le compteur m_compteRoueCodeuse++; et m_compteRoueCodeuse--; de la classe JlmRotaryEncoder
/// choisir entre un afficheur lcd I2C de type Digole (PICF182) ou de type LiquidCrystal (PCF8574)
#define LCD_LIQIDCRYSTAL  // utilisation de lcd liquid crystal I2C - PCF8574
/// Set the LCD address to 0x27 for a 16 chars and 2 line display pour pcf8574t / si pcf8574at alors l'adresse est 0x3f
//#define PCF8574AT // liquid crystal i2c avec pcf8574at @03f
#define PCF8574T // liquid crystal i2c avec pcf8574t @027
#define ROUE_CODEUSE_POSITION_DEFAUT_FIN_DE_COURSE_FERMETURE  30// initialisation par defaut au demarrage de la valeur de fin de course fermeture
/*--------------------------------------------------------------------------------*/
#endif

/**------Bibliothèque Flash pour mise en mémoire flash de l'arduino F()--------*/
#include <Flash.h>
#include <avr/pgmspace.h> // non nécessaire maintenant

#include "AA_fonctions.h" // prototypes des fonctions du programme

/** power and tools */
/** watchdog - Optimisation de la consommation */
#include "PowerTools.h"
#define DEBUG false // positionner debug pour l'utiliser ou pas
/*-----------------------------*/
#define WATCHDOG_BOUCLES 16 // nombre de boucles (16) du watchdog : environ 64s pour 8 boucles
/*-----------------------------*/
unsigned int memoireLibre = 0; // variable pour calcul de la memoire libre
volatile int f_wdt = 1; // flag watchdog
byte tempsWatchdog = WATCHDOG_BOUCLES ; // boucle temps du chien de garde
boolean reglage = false; // menu=false ou reglage=true
#define BUZZER true //positionner BUZZER en fonction de la presence ou pas d'un buzzer sur la carte (true = presence)
#define BUZZER_PIN 7 // broche du buzzer
PowerTools tools (BUZZER_PIN, BUZZER, DEBUG ); // objet tools et power

/** radio 433MHz */
#include "Radio.h"
#define RADIO_EMISSION  true  // positionner radio pour l'utiliser (true) ou pas
#define PIN_RADIO_EMISSION  10  // pin D10 emetteur radio
#define RADIO_TRANSMISSION_VITESSE  600 //initialisation de la bibliothèque avec la vitesse (vitesse_bps)
#define PIN_RADIO_EMISSION_SWITCH A2 // broche A2 en entree digitale pour le switch emission on/off
Radio radio(PIN_RADIO_EMISSION, PIN_RADIO_EMISSION_SWITCH, RADIO_TRANSMISSION_VITESSE, VW_MAX_MESSAGE_LEN, RADIO_EMISSION, DEBUG ); // classe Radio

/** led broche 13 */
#define LED_PIN 13

/** servo - montée et descente de la porte */
#include "ServoMoteur.h"
#define PIN_SERVO_CDE 8 // pin D8 cde du servo
#define PIN_SERVO_RELAIS 4 // pin D4 relais du servo
#define PIN_SECURITE_OUVERTURE 12 // pin D12 pour l'ouverture de porte
bool reduit = false; // vitesse du servo, normal ou reduit(false)
ServoMoteur monServo(PIN_SERVO_CDE, PIN_SERVO_RELAIS, PIN_SECURITE_OUVERTURE, SERVO_PULSE_STOP, SERVO_PULSE_OUVERTURE_FERMETURE, SERVO_PULSE_OUVERTURE_FERMETURE_REDUIT, DEBUG);

/** definitions */
#define MAX_CAD 1023  // maximum du convertisseur analogique digital
//https://www.carnetdumaker.net/articles/mesurer-la-tension-dalimentation-dune-carte-arduino-genuino-ou-dun-microcontroleur-avr/
//float tensionAlimentation = (MAX_CAD * 1.1) / tools.analogReadReference();

/** Accus */
#include "Accus.h"
#define PIN_ACCUS_N1  A6  //analog pin A6 : tension batterie N1
#define PIN_ACCUS_N2  A7  //analog pin A7 : tension batterie N2
#define ACCUS_TESION_MINIMALE  4.8 //valeur minimum de l'accu 4.8v
#define ACCUS_R1 4700 // resistance  R1 du pont
#define ACCUS_R2 10000 // resistance  R2 du pont
#define ACCU_N1 true  // batterie N1 presente si true
#define ACCU_N2 true // batterie N2 presente  si true
boolean batterieFaible = false; //  batterie < ACCUS_TESION_MINIMALE = true
Accus accusN1 (PIN_ACCUS_N1, OFFSET_AREF, ACCUS_TESION_MINIMALE, ACCUS_R1, ACCUS_R2, MAX_CAD, DEBUG );
Accus accusN2 (PIN_ACCUS_N2, OFFSET_AREF, ACCUS_TESION_MINIMALE, ACCUS_R1, ACCUS_R2, MAX_CAD, DEBUG );

/** encodeur rotatif */
#include "JlmRotaryEncoder.h"
#define SECURITE_TEMPS_FERMETURE  300 // utilisation du temps de descente pour la sécurité =  SECURITE_TEMPS_FERMETURE * les pas du codeur rotatif
#define SECURITE_TEMPS_OUVERTURE  300 // utilisation du temps de monté pour la sécurité =  SECURITE_TEMPS_OUVERTURE * les pas du codeur rotatif
#define ROUE_CODEUSE_POSITION_OUVERTURE_INITIALISATION 100 // initialisation de la position de l'encodeur rotatif avec le contact reed
#define ROUE_CODEUSE_POSITION_DEFAUT_INITIALISATION   150  // initialisation par defaut au demarrage de la possition de la roue codeuse 
// définition des pin pour le KY040
#define ENCODER_PIN_A   2   // A
#define ENCODER_PIN_B   11   // B
// classe encodeur rotatif KY040
JlmRotaryEncoder rotary(ENCODER_PIN_A, ENCODER_PIN_B, ROUE_CODEUSE_POSITION_DEFAUT_FIN_DE_COURSE_FERMETURE, ROUE_CODEUSE_POSITION_OUVERTURE_INITIALISATION, ROUE_CODEUSE_POSITION_DEFAUT_INITIALISATION); // clearButton si besoin
volatile bool interruptEncodeur = false; // valider la prise en compte de l'interruption
volatile unsigned long debutTempsEncodeur = 0; // utilisation de millis()

/** lumiere */
#include "Lumiere.h"
#define PIN_LUMIERE A0  //analog pin A0 : luminosite
#define LDR_R2 10000 // resistance  R2 du pont avec la LDR
#define LUMIERE_HEURE_FENETRE_SOIR  17  //horaire de la fenetre de non declenchement lumiere si utilisation horaire : 17h
#define LUMIERE_MATIN  330  // valeur de la lumière du matin
#define LUMIERE_SOIR  40  // valeur de la lumiere du soir
Lumiere lum(PIN_LUMIERE, LUMIERE_MATIN , LUMIERE_SOIR, LUMIERE_HEURE_FENETRE_SOIR, LDR_R2, MAX_CAD, LUMIERE_BOUCLES, DEBUG ); // objet lumiere

/** interruptions */
volatile boolean interruptBp = false; // etat interruption entree 9
volatile boolean interruptRTC = false; // etat interruption entree 5
volatile boolean interruptOuvBoi = false; // etat interruption entree 6
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
void loop() {

  lectureClavier(); // lecture du clavier
  temporisationAffichage(LCD_AFFICHAGE_TEMPS_BOUCLE) ; // temporisation pour l'affichage

  //reglages
  reglageTime(); // reglages de l'heure, minute, seconde si touche fleche droite
  reglageDate(); // reglage de la date si touche fleche droite
  reglageHeureOuverture();// reglage de l'heure d'ouverture
  reglageHeureFermeture();// reglage de l'heure de fermeture
  choixOuvFerm (); // choix de l'ouverture et la fermeture
  choixLumMatin();//  reglage de la lumiere du matin
  choixLumSoir();//  reglage de la lumiere du soir
  regFinDeCourseFermeture(); // reglage fin de course fermeture
  regFinDeCourseOuverture(); // reglage fin de course ouverture
  eclairageAfficheur(); // retro eclairage de l'afficheur

  if (SERVO_TEST) {
    testServo(); // reglage du servo plus test de la roue codeuse et du servo, à l'aide de la console
  }

  radio.testSwitchEmissionRadio(); // test du switch emission radio on/off

  memoireLibre = freeMemory(); // calcul de la  memoire sram libre

  ouvFermLum() ;  // ouverture/fermeture par test de la lumière

  // test suivant le nombre de batteries presentes
  if (ACCU_N1 and ACCU_N2) {
    batterieFaible = accusN1.accusFaible() or accusN2.accusFaible(); // test de la tension des batteries
  } else if (ACCU_N1) {
    batterieFaible = accusN1.accusFaible() ;// test de la tension de la batterie N1
  } else if (ACCU_N2) {
    batterieFaible = accusN2.accusFaible() ;// test de la tension de la batterie N2
  }

  ouverturePorte();
  fermeturePorte();

  /* pas de l'encodeur RISING */
  if (interruptEncodeur) {
    if ((millis() - debutTempsEncodeur) > TEMPO_ENCODEUR ) {
      rotary.compteurRoueCodeuse(SENS); // mis à jour du compteur de l'encodeur rotatif
      interruptEncodeur = false; // autorisation nouvelle it
    }
  }

  routineTestFermetureBoitier(); // test fermeture boitier
  routineTestOuvertureBoitier();// test ouvertuer boitier

  routineInterruptionBp(); // routine interruption Bp

  routineInterrruptionAlarme2() ; // routine alarme 2
  routineInterruptionAlarme1(); // routine alarme 1

  routineGestionWatchdog(); // routine de gestion du watchdog
}

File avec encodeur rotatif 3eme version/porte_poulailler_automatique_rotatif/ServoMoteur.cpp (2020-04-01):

/** ServoMoteur.cpp
  définitions de la classe ServoMoteur
  gestion du servo moteur au travers de la bibliothèque ServoTimer2
*/

#include "ServoMoteur.h"

//constructeur avec debug si nécessaire
ServoMoteur::ServoMoteur( byte pinCde, byte pinRelais, const byte pinSecuriteHaute, const int pulseStop, const int pulseOuvFerm ,
                          const int pulseReduit, const boolean debug) :  m_pinCde(pinCde), m_pinRelais(pinRelais),
  m_pulseStop(pulseStop),  m_pulseOuvFerm(pulseOuvFerm), m_pinSecuriteHaute(pinSecuriteHaute),
  m_pulseReduit(pulseReduit), m_debug(debug), m_pulse(pulseStop), m_ouvFerm(false), m_servoAction(false), m_debutTemps(0), m_tempsTotal(0)
{
}

ServoMoteur::~ServoMoteur()
{
}

///-----initialisation-----
void ServoMoteur::init () {
  digitalWrite(m_pinRelais, LOW); // mise hors tension du relais du servo (activation resistance de rappel avant l'activation de la broche de sortie)
  pinMode(m_pinRelais, OUTPUT); // relais servo's pin  an OUTPUT (pour eviter de cliqueter le relais)
  ServoTimer2::attach(m_pinCde); // use digital pin for commande du servo
  // on démarre à une valeur censée être la moitié de l'excursion totale de l'angle réalisé par le servomoteur
  ServoTimer2::write(m_pulseStop);  // value should usually be 750 to 2200 (environ 1500 = stop)

}

///------mise sous tension du servo et ouverture fermeture de la porte-------
// value should usually be 500 to 2500 (1280 = stop)
void ServoMoteur::servoOuvFerm(boolean batterieFaible, bool reduit)
{
  if (!batterieFaible and  !m_servoAction) { // si la batterie n'est pas faible et le servo non en action
    ServoMoteur::relaisSousTension(); // relais sous tension
    modificationVitesse(reduit);
  //  delay(200);// attente mise sous tension
    m_servoAction = true; // servo en action
  }
}

///------modificaton de la vitesse si le servo en action-------
// value should usually be 500 to 2500 (1280 = stop)
void ServoMoteur::servoVitesse( bool reduit)
{
  if (m_servoAction ) {
    modificationVitesse(reduit);
  }
}

///-----modification de la vitesse-----
void ServoMoteur::modificationVitesse( bool reduit) {
  // modification vitesse ouverture : 1500 - 140  / fermeture : 1500 + 140
  if (reduit) m_pulse = m_pulseOuvFerm; else m_pulse = m_pulseReduit;
  if (m_ouvFerm) ServoTimer2:: write(m_pulse = m_pulseStop - m_pulse); else ServoTimer2:: write(m_pulse = m_pulseStop + m_pulse);
}

///-----mise hors tension relais du servo-----
unsigned int ServoMoteur::servoHorsTension (unsigned int compteRoueCodeuse, unsigned int finDeCourse) {
  ServoMoteur::relaisHorsTension(); // relais hors tension
  if (!digitalRead(m_pinSecuriteHaute)) {
   // delay(200); // attente fin de l'arrêt complet du servo
    m_servoAction = false; // servo arrêt
    return finDeCourse;
  } else {
    m_servoAction = false; // servo arrêt
    return compteRoueCodeuse;
  }
}

///-----relais sous tension-----
void ServoMoteur::relaisSousTension() {
  digitalWrite(m_pinRelais, HIGH);
   ServoTimer2::write(m_pulseStop);  // value should usually be 750 to 2200 (environ 1500 = stop)
  m_debutTemps  = millis();// pour le calcul tu temps de montée ou descente
}

///-----relais hors tension-----
void ServoMoteur::relaisHorsTension () {
  ServoTimer2::write(m_pulseStop);  // value should usually be 750 to 2200 (environ 1500 = stop)
  digitalWrite(m_pinRelais, LOW);
  m_tempsTotal = millis() - m_debutTemps; // calcul tu temps en la mise sous tension du relais et la mise hors tension;
  if (m_ouvFerm) !m_ouvFerm; else m_ouvFerm;
}

//-----accesseur - getter-----
int ServoMoteur::get_m_pulse() {
  return m_pulse;
}

//-----mutateur - setter-----
void ServoMoteur::set_m_pulse(int pulse) {
  m_pulse = pulse;
}

//-----accesseur - getter-----
bool ServoMoteur::get_m_ouvFerm() {
  return m_ouvFerm;
}

//-----mutateur - setter-----
void ServoMoteur::set_m_ouvFerm(bool ouvFerm) {
  m_ouvFerm = ouvFerm;
}

//-----accesseur - getter-----
bool ServoMoteur::get_m_servoAction() {
  return m_servoAction;
}

//-----mutateur - setter-----
void ServoMoteur::set_m_servoAction(bool servoAction) {
  m_servoAction = servoAction;
}

//-----mutateur - setter-----
unsigned int ServoMoteur::get_m_tempsTotal() {
  return m_tempsTotal;
}

//-----mutateur - setter-----
void ServoMoteur::set_m_tempsTotal(unsigned int tempsTotal) {
  m_tempsTotal = tempsTotal;
}

//-----mutateur - setter-----
unsigned long ServoMoteur::get_m_debutTemps() {
  return m_debutTemps;
}

//-----mutateur - setter-----
void ServoMoteur::set_m_debutTemps(unsigned long debutTemps) {
  m_debutTemps = debutTemps;
}

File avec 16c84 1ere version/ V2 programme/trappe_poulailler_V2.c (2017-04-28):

// commande d'ouverture v2.1
// date 25.01.2011
// gestion de la ldr par ampli ops
// pour la trappe du poulailler
// avec servo moteur
// et ldr pour la lumière
// compiler cc5x
#pragma chip PIC16F84A
//config _CP_OFF & _WDTE_OFF & _PWRTE_ON & _FOSC1-FSOC0_HS
#pragma config |= 0x3ff2
#include "int16CXX.h"
int compteur2;
long compteur1;
int sens;
bit signal;
bit etat;
bit servo_sous_tension;
bit tant_que;
long compteurdelay;
int defaut;
long tempsdelay;

int av;
int ar;
int stop;


// interruption
#pragma origin 4
interrupt inter_50(void) // pour cde sevo
{
int_save_registers // + autres si necessaire (option, FSR...)
TMR0 = 233;
if (servo_sous_tension == 1) {
if (++compteur1==360) {
compteur1=0;
compteur2=0;
signal = 1;

}
else {
if (signal == 1) {
if (compteur2 == sens) {
signal = 0;
PORTB.1=0;
}
else{
PORTB.1=1;
compteur2++;
}
}
}
}
compteurdelay++; // pour delay
if (PORTB.6 == 1) { // led clignotante
PORTB.6 = 0;
}
else {
PORTB.6 = 1;
}
T0IF = 0;
int_restore_registers
}

// fonction delay
void delay_s (long tempsdelay)
{
compteurdelay = 0;
while (compteurdelay <= tempsdelay) {
}
}

// fonction sleep avec reveil sur front descendant
void sleepfrontdescendant (void)
{
INTCON = 0b00010000; // bit INTE à 1 pour it sur front sur rb0
OPTION = 0b10000000; // bit INTEDG à 0 pour front descendant sur rb0
PORTB.6 = 0;
sleep();
INTCON = 0b10100000;
OPTION = 0b11000000;
}

// fonction ouverture
void ouverture (void)
{
if (PORTB.5 == 0) { // contacteur haut = 1 ouverture - trappe basse
PORTA.2 = 1; // cde relais
delay_s(10000);
sens = av;
servo_sous_tension = 1;
compteurdelay = 0;
defaut = 0;
while (PORTB.5 == 0 && defaut < 7)  {
if (compteurdelay == 20000) { // arrêt de securité
compteurdelay = 0;
defaut ++;
}
}
if (defaut == 7 ) {   // en mode automatique ou manuel
servo_sous_tension = 0;
PORTB.1 = 0;
PORTA.2 = 0;
T0IE = 0;
PORTB.6 = 0;
sleep();  // arrêt en mode sommeil (il faut une RAZ pour en sortir)
while (tant_que == 0) {
}
}
else {
sens = stop;
servo_sous_tension =0;
PORTA.2 = 0; // cde relais
}
}
}

// fonction fermeture
void fermeture (void)
{
if (PORTB.2 == 0) {  // contacteur bas  -  trappe haute
PORTA.2 = 1; // cde relais
delay_s(10000);
sens = ar;
servo_sous_tension = 1;
compteurdelay = 0;
defaut = 0;
while (PORTB.2 == 0 && defaut < 6) {
if (compteurdelay == 20000) {  // arrêt de sécurité
compteurdelay = 0;
defaut ++;
}
}
if (defaut == 6 && PORTB.4 == 0) {  // manuel
servo_sous_tension = 0;
PORTB.1 = 0;
PORTA.2 = 0;
T0IE = 0;
PORTB.6 = 0;
sleep();  // arrêt en mode sommeil (il faut une RAZ pour en sortir)
while (tant_que == 0) {
}
}
else {
sens = stop;
servo_sous_tension = 0;
PORTA.2 = 0; // cde relais
}
}
}

// programme
void main (void)
{
INTCON = 0b10100000; //bits GIE et T0IE à 1 pour utiliser l'interruption du timer
OPTION = 0b11000000;  // 
TRISB = 0b10111101;  // b6 et b1 en sortie
TRISA = 0b11111011;  // a2 en sortie
PORTB.6 = 1; // led
PORTA.2 = 0; // cde relais
PORTB.1 = 0; // cde servo moteur à 0
servo_sous_tension = 0;
signal = 1;  
etat = 1;
tant_que = 0;
av = 31;  // avant
ar = 21;  // retour
stop = 0;  // stop à 0
sens = stop;
compteur1 = 0;
compteur2 = 0;

// Fin des inits et debut du programme principal 

while (tant_que == 0) {

if (PORTB.4 == 0) { // manuel
delay_s(20000);
if (PORTB.4 == 0) {
if (PORTB.3 == 0) { // montée
delay_s(10000);
if (PORTB.3 == 0) {
ouverture();
}
delay_s(20000);
}
else {
if (PORTB.7 == 0) { // descente
delay_s(10000);
if (PORTB.7 == 0) {
fermeture();
}
delay_s(20000);
}
}
}
}

else {  // automatique
delay_s (20000);
if (PORTB.4 == 1 ) {  // automatique rb4 = 1
if (PORTB.5 == 1 ) {  // trappe haute rb5 = 1
if (PORTA.4 == 1 ) {  // ldr haut = 1, ra4 = 1
sleepfrontdescendant();
}
else {
if (PORTB.0 == 1 ) {  // ldr ou =1, rb0 = 1
sleepfrontdescendant();
}
else {
fermeture();
sleepfrontdescendant();
}
}
}
else {
if (PORTB.2 == 1 ) {  // trappe basse rb2 = 1
if (PORTA.4 == 0 ) {  // ldr haut = 0, ra4 = 0
sleepfrontdescendant();
}
else {
ouverture();
sleepfrontdescendant();
}
}
else {
if (PORTA.4 == 1 ) {  //  ldr haut = 1
ouverture();
sleepfrontdescendant();
}
else {
sleepfrontdescendant();
}
}
}
delay_s (20000);
}
}
}
}

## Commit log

2016-12-01 schéma, organigramme, plans 3d, manuel d'utilisation
    [porte poulailler arduino ver 1-4.sch, porte_poulailer_couronne_fixed.stl, porte_poulailer_fixed.stl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]
2016-12-02 correction nom fichiers
    [porte_poulailer_couronne_fixed.stl, porte_poulailer_fixed.stl, porte_poulailer_rondelle_fixed.stl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]
2016-12-02 coorections noms de fichiers
    [porte_poulailler_couronne_fixed.stl, porte_poulailler_fixed.stl, porte_poulailler_rondelle_fixed.stl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]
2016-12-13 pb ouverture fermeture - // sur sens dans servo.h - erreur dans la routine it roue codeuse - nettoyage
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2016-12-18 Le message radio est correct, mais je ne sais pas pourquoi j'ai un trou en case une au deuxième tour git status!
2016-12-19 test de l'ouverture du boitier pour eviter de remplir le tableau du message radio sans l'envoi
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2016-12-22 fin de la classe servoMoteur - il rest un soucis avec la touche 5
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2017-01-12 boutons integres dans la classe Clavier - bon fonctionnement - pb à régler : Bp montée ou descente avec au moins deux apuuis succesifs - consommation avec affichage 55ma - consommation sans affichage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
2017-01-12 debut branche menu
    [porte_poulailler_support_ecran_fixed.stl]
2017-01-13 correction bug affichage ouverture boitier
    [LcdDigoleI2C.cpp]
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2017-01-27 passage de l'adresse du boitier 24C32 par le constructeur de la classe HorlogeDS3232 car le boitier memoire est sur la meme carte
2017-01-27 texte à l'ouverture et la fermeture du boitier - envoyé par radio - bon fonctionnement de l'ensemble
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2017-01-27 class HologeDS3232 - ajout du reglage des times et date - bon fonctionnement
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2017-01-30 modification du fichier porte_poulailler_fixed_stl
    [porte_poulailler_fixed.stl]
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2017-02-03 modifications des fichiers stl pour la fermeture du boitier et le bon positionnement de l'encodeur rotatif
    [porte_poulailler_fixed.stl, porte_poulailler_rondelle_fixed.stl, porte_poulailler_support_ecran_fixed.stl]
2017-02-04 retour sur la modification des fichiers stl pour la fermeture du boitier - remplacée par la découpe du pcb
    [porte_poulailler_rondelle_fixed.stl, porte_poulailler_support_ecran_fixed.stl]
2017-02-04 ajustements du support ecran
    [porte_poulailler_support_ecran_fixed.stl]
2017-02-04 ajout d'un commutateur avec ou sans emission radio
    [porte poulailler arduino ver 1-4.sch]
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2017-02-06 support boitier pour sa fixation
    [support_boitier_fixed.stl]
2017-02-08 modification des entrees A2 et A3 vers A6 et A7 pour utiliser la broche A2 en entree numerique
    [porte poulailler arduino ver 1-4.sch]
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2017-02-10 ajout condensateur 100nf pour les parasites du Bp, et modification du schéma électrique
    [porte poulailler arduino ver 1-4.sch]
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2017-02-16 modification fichier freecad support boitier
    [support_boitier_fixed.stl]
2017-02-21 modification du support boitier : renfort - retour arriere pour le bp : pb
    [support_boitier_fixed.stl]
2017-02-21 modifications schema électrique
    [porte poulailler arduino ver 1-4.sch]
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2017-02-25 modification du support interne pour rtc et reed
    [porte_poulailler_fixed.stl]
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2017-02-27 modifications fichiers freecad - solidité
    [porte_poulailler_fixed.stl, porte_poulailler_rondelle_fixed.stl, porte_poulailler_support_ecran_fixed.stl]
2017-02-28 modifications fichiers freecad - ajustements
    [porte_poulailler_fixed.stl]
2017-03-01 modifications fichiers freecad - passages cables
    [porte_poulailler_fixed.stl]
2017-03-02 modifications fichiers freecad - pour switch reed
    [porte_poulailler_fixed.stl]
2017-03-03 modifications fichiers freecad - fenetre pour blocage batteries
    [porte_poulailler_fixed.stl]
2017-03-03 modifications fichiers freecad - support batteries avec rilsan
    [porte_poulailler_fixed.stl]
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2017-03-22 modification fichier freecad support reeds
    [porte_poulailler_fixed.stl]
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2017-04-25 ecartement du lcd de la carte principale
    [porte_poulailler_support_ecran_fixed.stl]
2017-04-25 amenagement des dossiers
    [porte_poulailler_couronne_fixed.stl, porte_poulailler_fixed.stl, porte_poulailler_rondelle_fixed.stl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]
2017-04-26 ajustements et protection contre la pluie
    [porte_poulailler_fixed.stl, porte_poulailler_rondelle_fixed.stl, porte_poulailler_support_ecran_fixed.stl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]
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2017-04-30 impresion 3d - ajustements pour la fermeture du boitier
    [porte_poulailler_rondelle_fixed.stl, porte_poulailler_support_ecran_fixed.stl]
2017-05-01 butoir pour la porte
    [butoir_fixed.stl]
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2017-05-06 mise à jour du readme et arrangement des dossiers
    [butoir_fixed.stl, porte_poulailler_couronne_fixed.stl, porte_poulailler_fixed.stl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]
2017-06-14 ver 2.0.1 juin 2017, modification du menu et correction dela classe lumiere
    [LcdPCF8574.cpp, Lumiere.cpp, porte_poulailler_automatique_rotatif.ino]
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2017-06-24 modification support boitier, et creation protection pluie
    [support_boitier_fixed.stl, support_boitier_haut_fixed.stl, support_boitier_protection_haute_fixed.stl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]
2017-06-24 support panneau solaire
    [support_solar_pannel_fixed.stl]
2017-06-29 documentation et pcb à l'aide de kicad
    [support_solar_pannel_fixed.stl]
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2017-07-12 ajustument de la couronne _ profondeur pour l'adaptateur
    [porte_poulailler_couronne_fixed.stl]
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2017-07-19 test du buzzer avant fermeture
    [Lumiere.cpp, porte_poulailler_automatique_rotatif.ino]
2017-07-20 buzzer deux fois max avant fermeture
    [Lumiere.cpp, porte_poulailler_automatique_rotatif.ino]
2017-07-21 buzzer dans la routine watchdog
    [Lumiere.cpp, porte_poulailler_automatique_rotatif.ino]
2017-07-22 buzzer : augmantation du nb de sonneries. pb batteries faibles : ajout N boitier
    [porte_poulailler_automatique_rotatif.ino]
2017-07-23 3 sonneries avant fermeture, parametre presence buzzer sur la carte, buzzer 2s
    [Lumiere.cpp, porte_poulailler_automatique_rotatif.ino]
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2017-07-24 gestion du buzzer dans la classe tools
    [PowerTools.cpp, porte_poulailler_automatique_rotatif.ino]
2017-07-25 numero du boitier avant chaque message, pb routine buzzer après un message radio ???, schema avec le buzzer et sa diode sur la broche D7.
    [Lumiere.cpp, PowerTools.cpp, porte_poulailler_automatique_rotatif.ino]
2017-07-26 buzzer sur le boitier n001 , mise à jour du programme v2.0.2 avec prise en compte du buzzer, reglages parametres pour le boitier n001
    [Clavier.cpp, JlmRotaryEncoder.cpp, porte_poulailler_automatique_rotatif.ino]
2017-07-26 version v2.0.2 avec prise en compte du buzzer
    [JlmRotaryEncoder.cpp, porte_poulailler_automatique_rotatif.ino]
2017-07-28 nouvelle glissiere avec supports en 3d
    [butoir_fixed.stl, support_glissiere_droite_fixed.stl, support_glissiere_gauche_fixed.stl]
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2017-08-07 corrections defauts de syntaxe
    [porte_poulailler_automatique_rotatif.ino]
2017-08-07 declenchement buzzer compteurWatchdogLumiere > 1
    [porte_poulailler_automatique_rotatif.ino]
2017-08-09 corrections erreurs de compilation sans consequences du programme : recepteur
    [Clavier.cpp, JlmRotaryEncoder.cpp, Lumiere.cpp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]
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2017-08-11 correction de la gestion des tensions des accus
    [porte_poulailler_automatique_rotatif.ino]
2017-08-11 corrections petits defauts renvoyés par le compilateur
    [Clavier.cpp, LcdDigoleI2C.cpp, LcdPCF8574.cpp]
2017-08-12 declenchement buzzer compteurWatchdogLumiere > 2 (eviter declenchements non desires)
    [porte_poulailler_automatique_rotatif.ino]
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2017-08-28 correctif pour le fonctionnement du buzzer
    [Lumiere.cpp, porte_poulailler_automatique_rotatif.ino]
2017-10-11 mise à jour boitier 4 sans le buzzer
    [porte_poulailler_automatique_rotatif.ino]
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2017-10-14 buzzer sur boitier n04
    [porte_poulailler_automatique_rotatif.ino]
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2017-10-29 freecad - cle ouverture boitier et modification support panneau
    [cle_ouverture_boitier_fixed.stl, support_solar_pannel_fixed.stl]
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2017-12-20 modification du declenchement du buzzer. pb avec les messages radio
    [porte_poulailler_automatique_rotatif.ino]
2017-12-21 le buzzer ne fonctionne maintenant que le soir por la rentree des poules
    [porte_poulailler_automatique_rotatif.ino]
2017-12-21 pb buzzer et radio
    [porte_poulailler_automatique_rotatif.ino]
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2017-12-22 ajout au declenchement du buzzer, le test de la porte ouverte.
    [porte_poulailler_automatique_rotatif.ino]
2018-01-12 correction tension de ref 1.1v du boitier n002
    [porte_poulailler_automatique_rotatif.ino]
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2018-04-26 probleme de reglages des valeurs ouverture et fermeture en negatif. provisoirement regle en initialisant les valeurs lors d'un reset du micro
    [JlmRotaryEncoder.cpp, porte_poulailler_automatique_rotatif.ino]
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2020-04-01 activation du buzzer pour le mode fermeture de la porte avec la lumiere
    [Lumiere.cpp, PowerTools.cpp, ServoMoteur.cpp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]
2021-10-18 mise a jour schemas
    [porte poulailler arduino rotary ver 2-0.sch]
